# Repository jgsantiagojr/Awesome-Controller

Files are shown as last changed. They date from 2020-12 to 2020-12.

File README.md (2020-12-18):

### Jamie's Awesome Power Controller

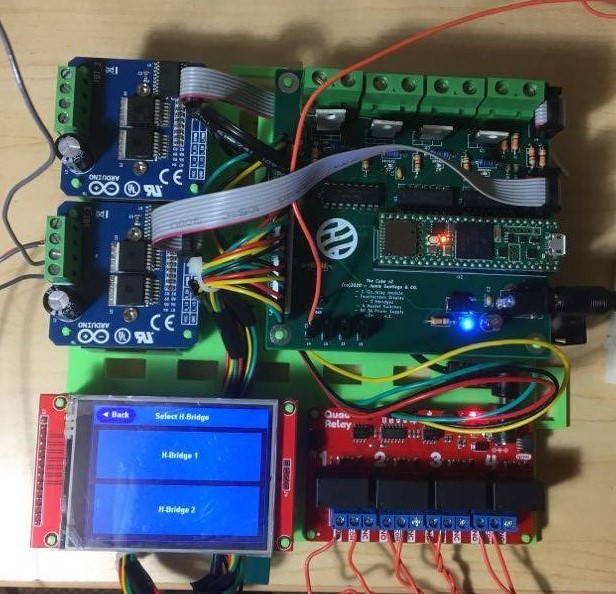
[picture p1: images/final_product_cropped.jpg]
final_product_cropped (https://youtu.be/NAIDJquwWuA "Demo Video")


Hi I'm Jamie! My Awesome Power Controller is a device that is controlled by a Teensy 4.1 and contains 2 H-Bridges, 4 MOSFET switches, and 4 Relays, as well as 4 General Purpose Input Outputs and a Touchscreen Display. Click on the image above for a demo!

The user can choose to either run a pre-written code option or control the different devices independently. An example of a pre-written code option is the Sensor Driven Motor. If the user selects this option, the controller will run a script that sets the PWM signal for H-Bridge 1 to the input from a sensor that is connected to GPIO 14. If the user chooses to control the devices independently then they will be able to individually toggle each of the relays, set the PWM values for each MOSFET switch and set the PWM values and direction for each H-Bridge. 

#### Suppliers

For my PCBs I used: JLCPCB

For my parts I used: Digikey, SparkFun and PJRC

#### Why this project?

This project was originally started for a class I took in the Fall of 2020, Microcontrollers for the Real World.  The point of this class was to be a remote, one-on-one session based class that would teach students to design and build a real-world controller using modular components. I decided that I wanted my project to be something that I could use for future projects and control high power systems with, so I decided to create this generic high power controller. 

#### The Process

##### The Start

The process for this project had a lot of ups and downs. I started off wanting to make everything from scratch and very poorly scoped expectations for what I could do in a semester. But after some initial designs and discussions as to why those designs wouldn't work or what could be better and cheaper, I ended up on a much cleaner path. 

My initial take on the project was that it could be board with a bunch of MOSFETs that the user could configure into different circuits (such as H-bridges and half-bridges) based on what they need to do. It was also supposed to be configurable from the users personal device via Bluetooth in addition to the on-board user interface. However, I quickly learned that this was unnecessarily complex and expensive, and way over-scoped for it to have a reasonable probability of success by the end of the semester. 

So I took a step back. Focused on other things for a day, and came back with a plan. I would use H-bridge modules and then simply have MOSFET switches available as well., in addition to my relay module and touchscreen display. 

##### Prototype 1

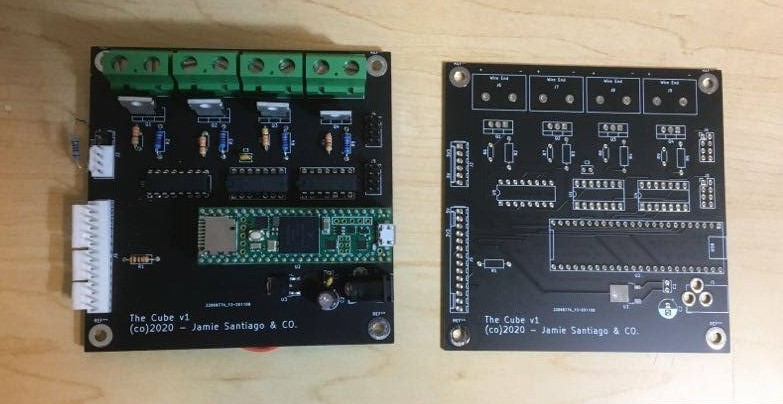
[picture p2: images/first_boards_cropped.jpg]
first_boards_cropped


So a week or two after I pivoted to a more module-focused path, I had my first PCBs shipped. After soldering them together, I saw a few obvious problems:

- There was no way to tell if things were working with just the board, so I needed to add indicator LEDs so I could know if the device I was controlling was working without having to plug in a power source or motor/multimeter and so I could easily tell when the board was on. 
- There was no easy way to connect to ground. When I was trying to test that the right pins were outputting the right things there was no easy ground pin to base the measurements off of. So I needed to add a GND pin. 
- There were no GPIO pins. Had to add those. 
- No ON/OFF Switch, it was on whenever I plugged it in. I didn't like this because I wanted the device to be a tool I could keep on the table-top and that I should be able to turn it off without unplugging it. 

There were also a few problems that weren't so obvious:

- I2C line didn't have pull-up resistors. This made it so the teensy couldn't identify the relay board that I was trying to communicate with. 
- I2C line and the SPI lines shared the SCK pin. This was a big error, since SCK is the SPI clock. I discovered this was the problem after soldering a jumper cable between an SCL pin on the teensy and the clock pin on the I2C line and things started working. So I needed to make sure the I2C line was connected to SCL not SCK.

After I fixed all of these problems in the schematic and updated the layout I was able to send out for my second boards. 

##### Prototype 2

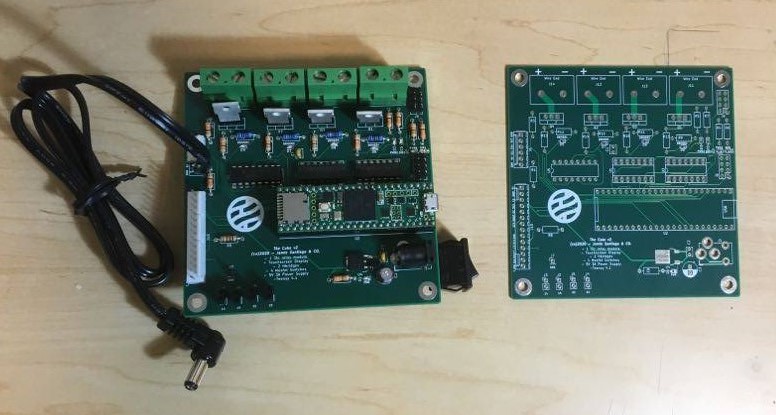
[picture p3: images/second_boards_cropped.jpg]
second_boards_cropped


My second boards were also my final boards. At the same time as ordering them I began designing my mechanical packaging.  The boards worked fairly well but still have a few bugs:

- Something is wrong with the power. Every once in a while the LCD display just shows the backlighting and the only way to fix it is by restarting the entire device. 
- The layout of the board is very awkward. I need to re-lay all the components so that the board integrated more seamlessly with its packaging.
- Having a 6 pin connector for I2C is inconvient when only 4 pins are needed for i2c and the other 2 are for board power. I need to change that from a 6 pin to a 4 pin with a 2 port wire-to-board screw terminal. 

Something that wasn't really a bug but still a pain was the LEDs. They all worked, but since they were tiny and surface mount they took forever to solder on. If there is space to use LEDs that are easier to solder on I need to incorporate them. 

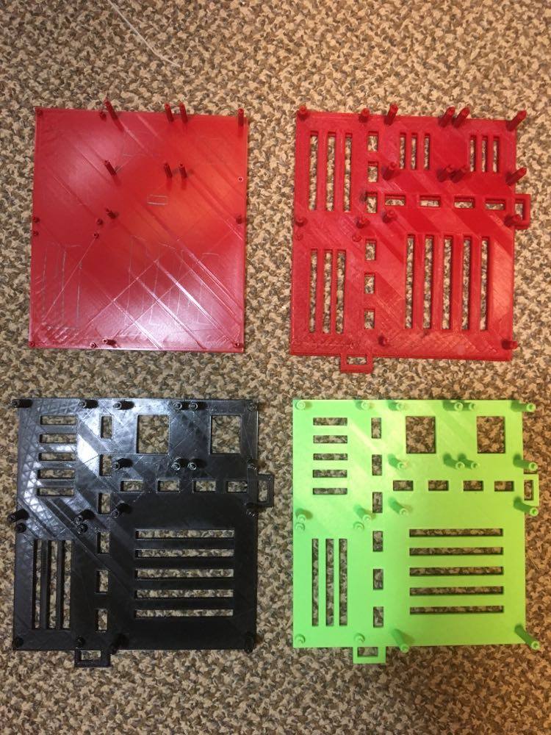
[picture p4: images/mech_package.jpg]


In terms of the mechanical packaging, my first attempt at a design was fun but didn't take into consideration that I would be 3D printing it, so I had to start from the beginning. For what would be my final package, I chose to have a simple plate and pegs to hold all of the modules secure next to each other in a clean way. 

I am proud to say that my second prototype works well and accomplishes what I wanted it to. I definitely learned a lot of circuit board design, mechanical packaging/3D printing and how to tie them in together.  

#### Parts List

| Part Name | Part Number | Price per unit | Distributer |
| --- | --- | --- | --- |
| 2 Pack BTS7940 High Power Driver Module | BTN7960 | 13.89 | Amazon |
| 4 Pack of female 8pos cables | | 8.75 | Amazon |
| 4 Pin Molex Connector | 22232041 | .28 | Digikey |
| 2 Position Wire to Board Terminal | 796739-2 | 1.69 | Digikey |
| 14 Pin Molex Connector | 22232141 | 1.56 | Digikey |
| Power Jack Connector | PJ-202A | .6 | Digikey |
| .1uF Capacitor | C320C104K5R5TA7303 | .22 | Digikey |
| 100uF Capacitor | JMK316ABJ107ML-T | .56 | Digikey |
| Level Converter 16DIP | CD40109BE | .55 | Digikey |
| 8 Position Headers for H-Bridge Module  | PPTC042LFBN-RC | .15 | Digikey |
| 24 Position Headers for Teensy | PPTC241LFBN-RC | 1.37 | Digikey |
| 100 Ohm Resistor | CFR-25JB-52-100R | .1 | Digikey |
| 330 Ohm Resistor | CFR-25JB-52-330R | .1 | Digikey |
| 10K Ohm Resistor | CFR-25JB-52-10K | .1 | Digikey |
| 3v3 1A voltage regulator | NCP1117DT33G | .44 | Digikey |
| 4 Pin Dual-Female Wire | 1597-1502-ND | 3.38 | Digikey |
| 2 Position Headers | S7000-ND | .306 | Digikey |
| LED BLUE CLEAR CHIP SMD | 160-1647-1-ND | .262 | Digikey |
| On-Off switch | 2449-RA1122DWR-ND | .98 | Digikey |
| DC Power Jack | 172-4207-ND | 3.47 | Digikey |
| LCD Touchscreen | DISPLAY_ILI9341_TOUCH | 15 | PJRC |
| Teensy 4.1 | | 26.95 | PJRC |
| Qwiic Quad Relay | COM-16566 | 29.95 | SparkFun |
| 60V N-Channel MOSFETs | FQP30N06L | .95 | SparkFun |

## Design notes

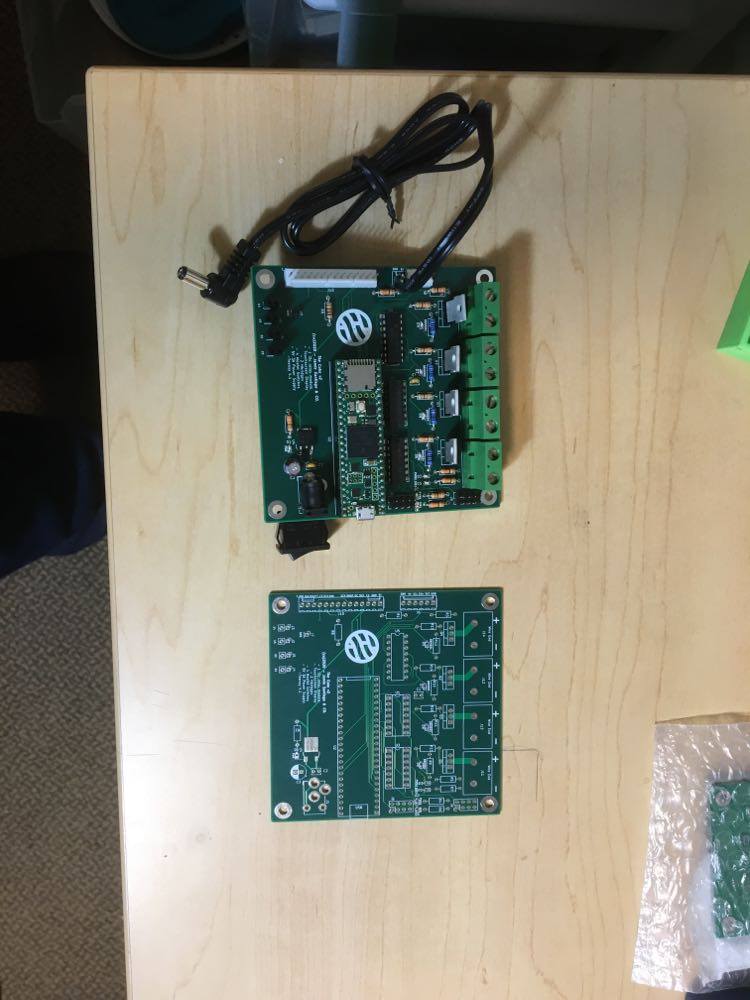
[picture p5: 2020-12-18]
images/second_boards.jpg

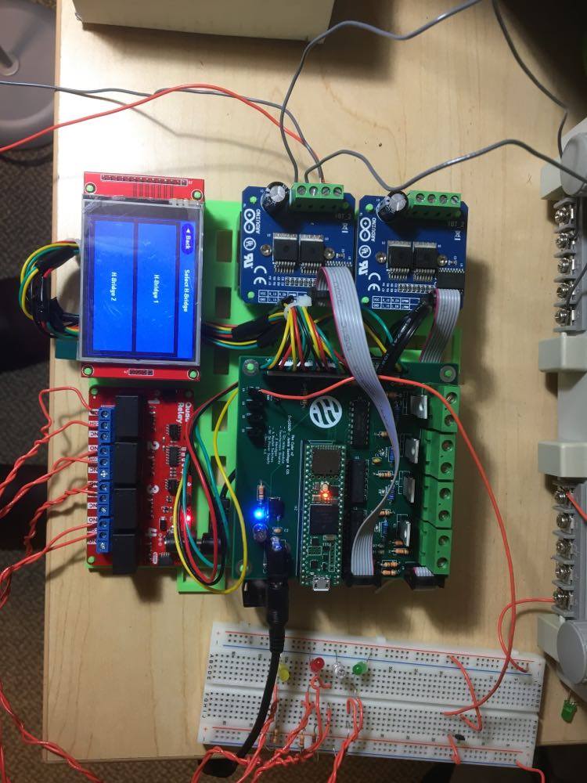
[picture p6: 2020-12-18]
images/final_product.jpg

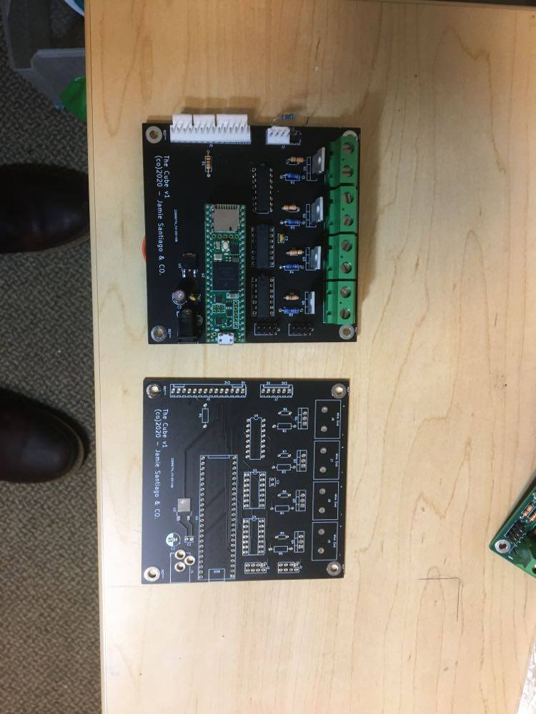
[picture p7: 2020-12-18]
images/first_boards.jpg

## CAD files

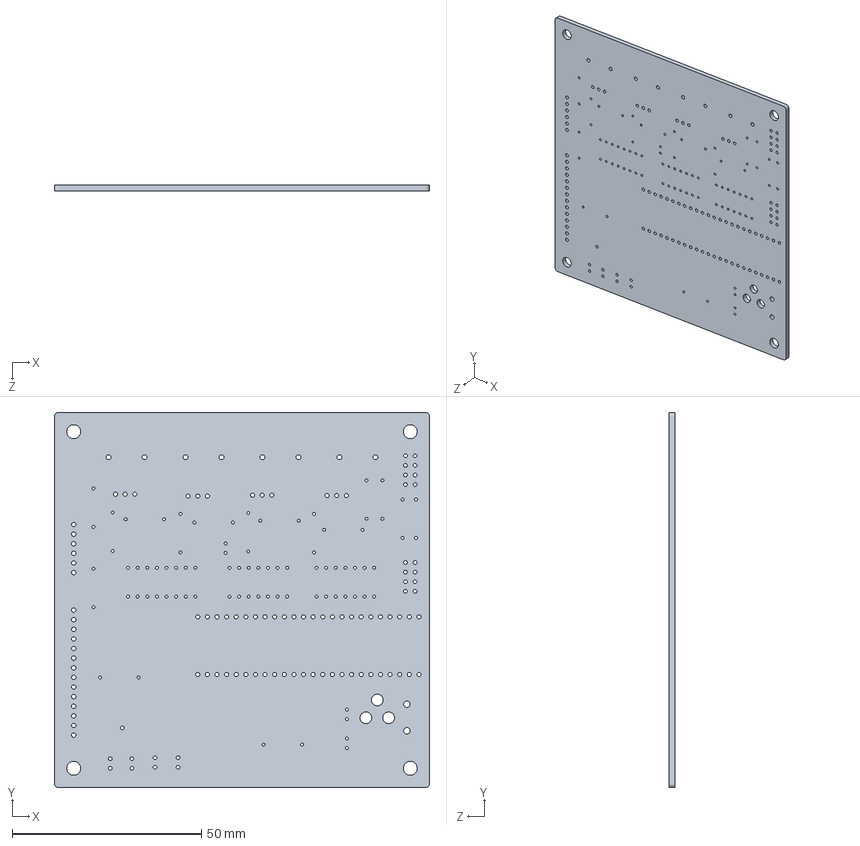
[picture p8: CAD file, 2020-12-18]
Mechanical/Generic_Controller_pcb.SLDPRT
99.1 x 99.1 x 1.60 mm

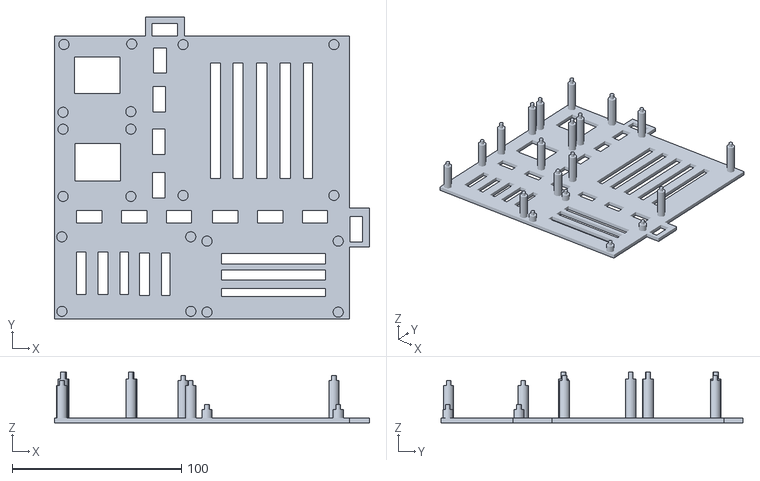
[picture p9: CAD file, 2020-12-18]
Mechanical/STLs/baseplatev5.STL
185.9 x 178.2 x 30.0

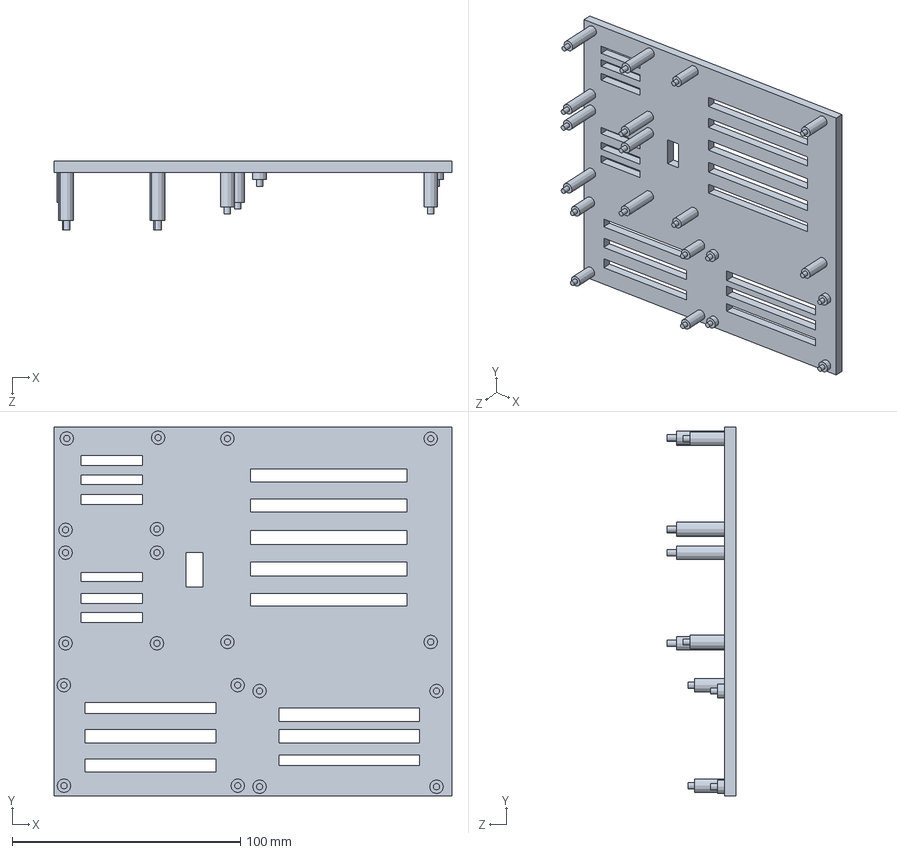
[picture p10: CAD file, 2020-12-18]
Mechanical/baseplate.SLDPRT
174.2 x 161.5 x 30.0 mm

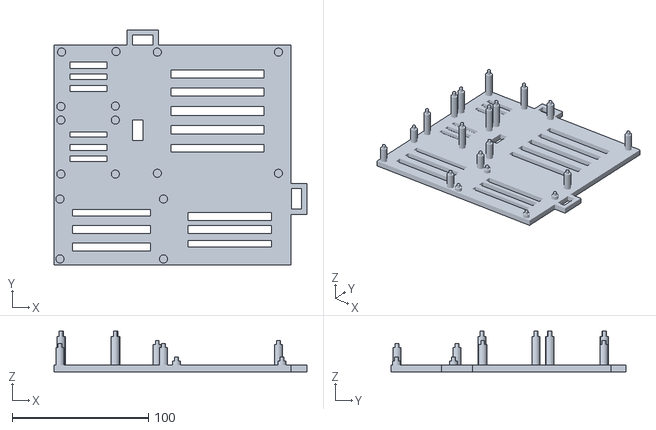
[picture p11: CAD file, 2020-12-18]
Mechanical/STLs/baseplatev2.STL
185.9 x 172.7 x 30.0

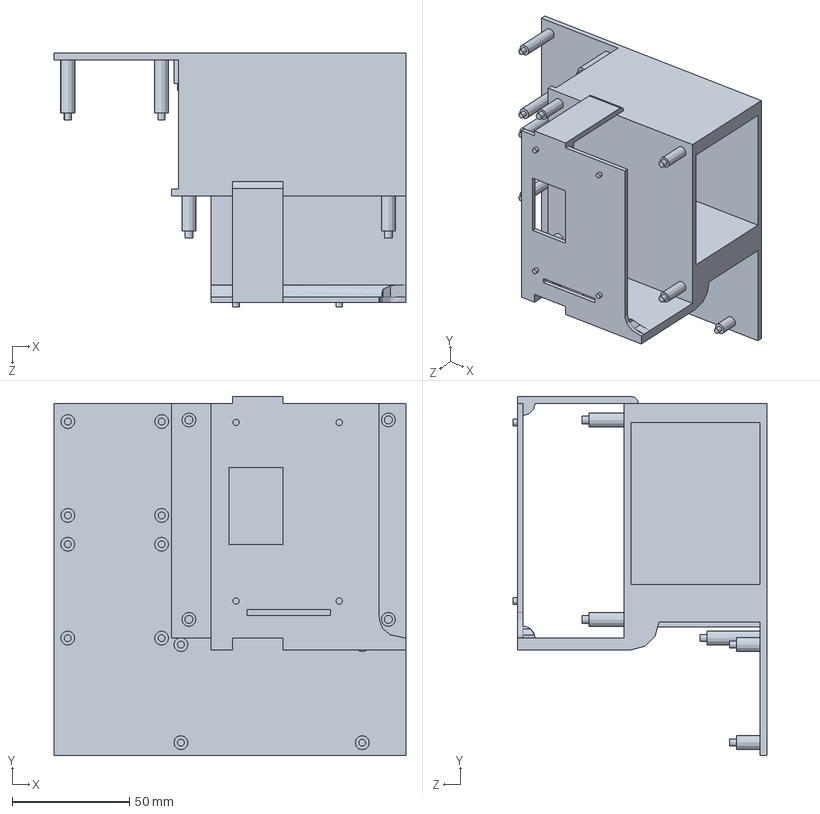
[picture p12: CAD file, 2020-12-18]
Mechanical/PyramidPackage.SLDPRT
150.0 x 153.0 x 108.4 mm

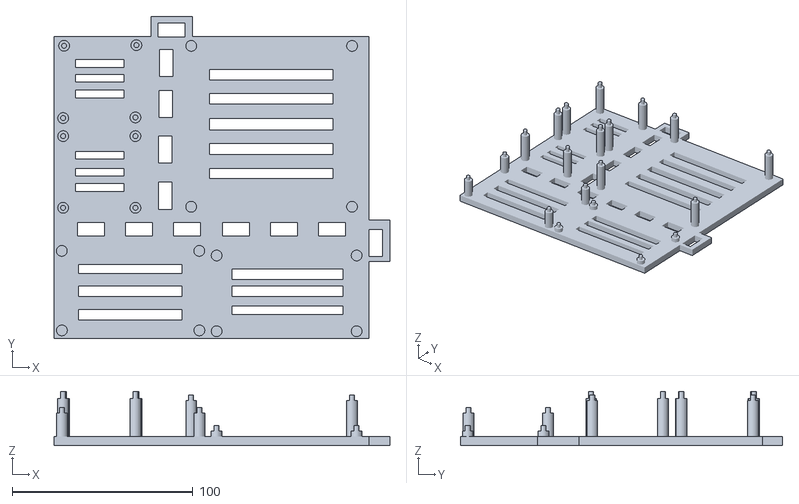
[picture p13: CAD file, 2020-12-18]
Mechanical/STLs/baseplatev4.STL
185.9 x 178.2 x 30.0

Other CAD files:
Mechanical/STLs/baseplatev6.STL
Mechanical/baseplatev3.SLDPRT
Mechanical/STLs/PyramidPackage.STL
Mechanical/STLs/baseplate.STL
Mechanical/STLs/baseplatev3.STL
Mechanical/module_layout.SLDDRW

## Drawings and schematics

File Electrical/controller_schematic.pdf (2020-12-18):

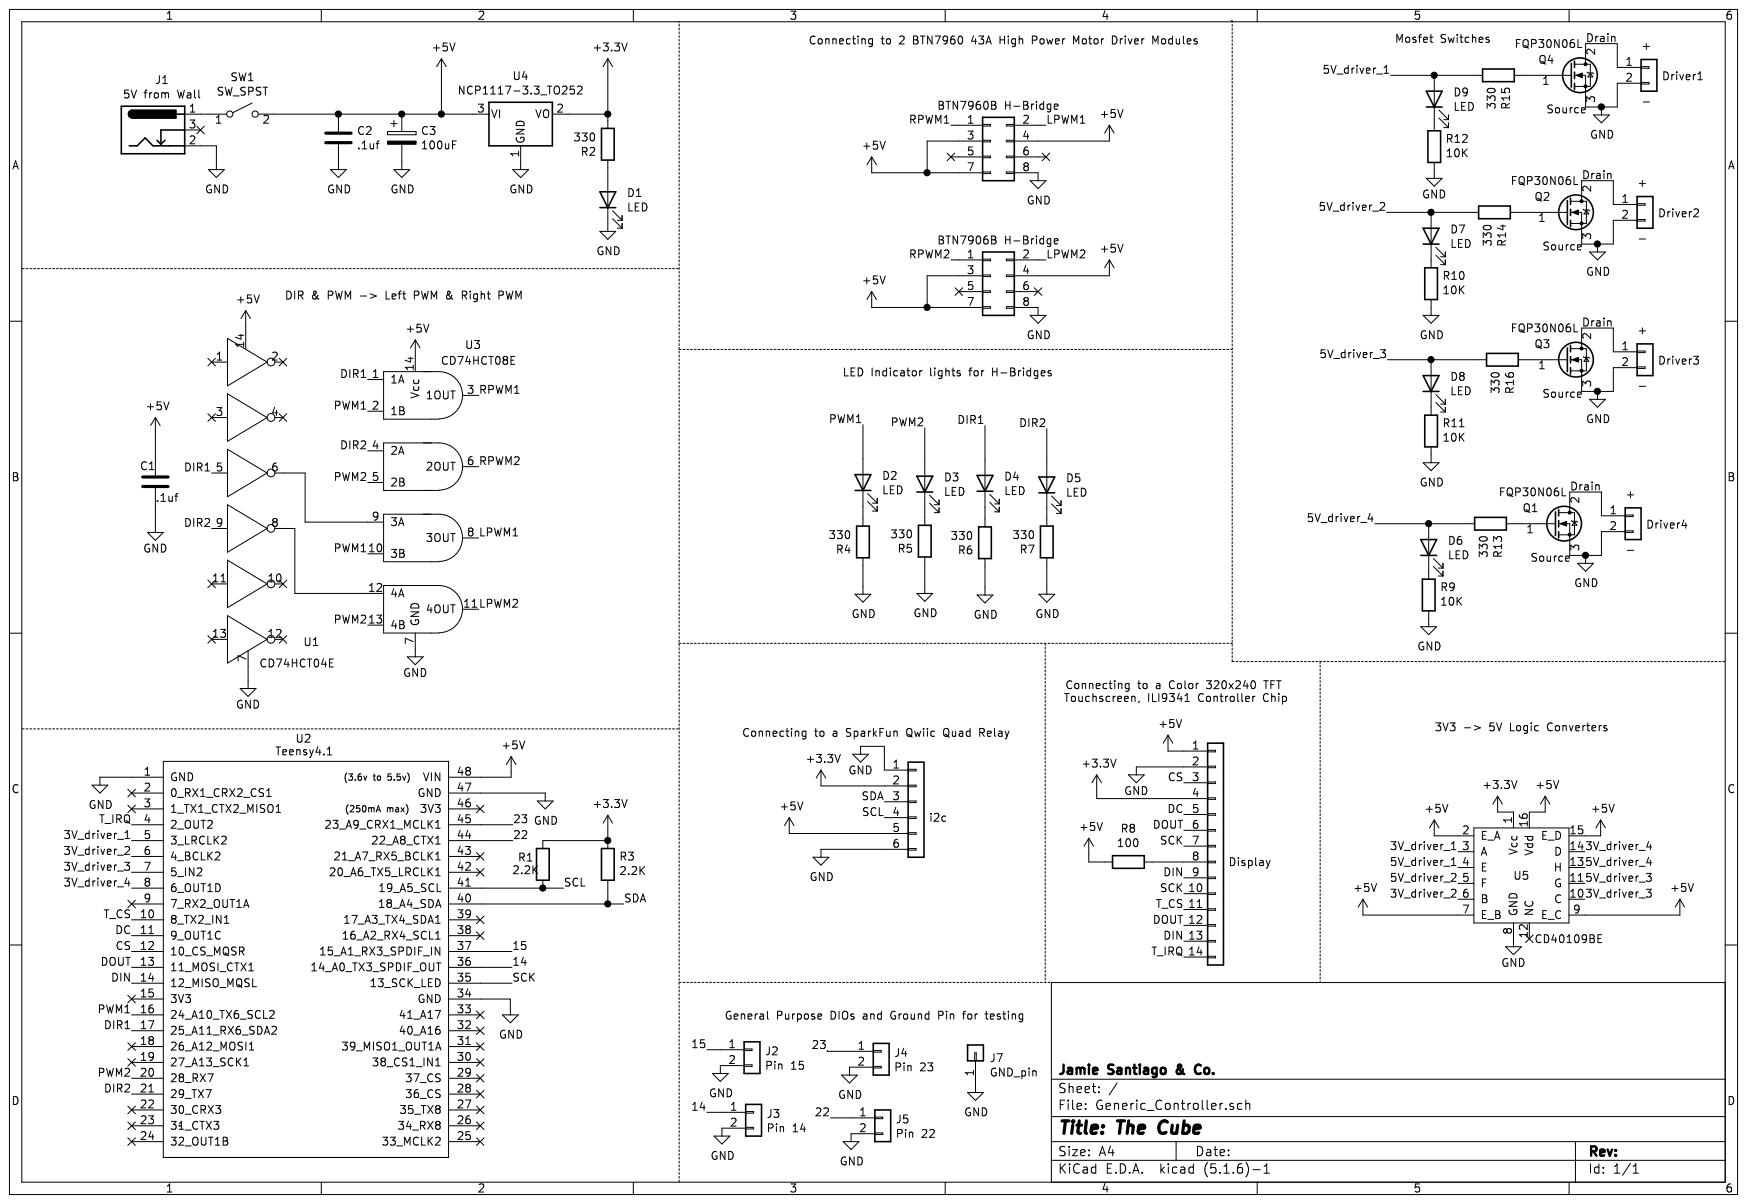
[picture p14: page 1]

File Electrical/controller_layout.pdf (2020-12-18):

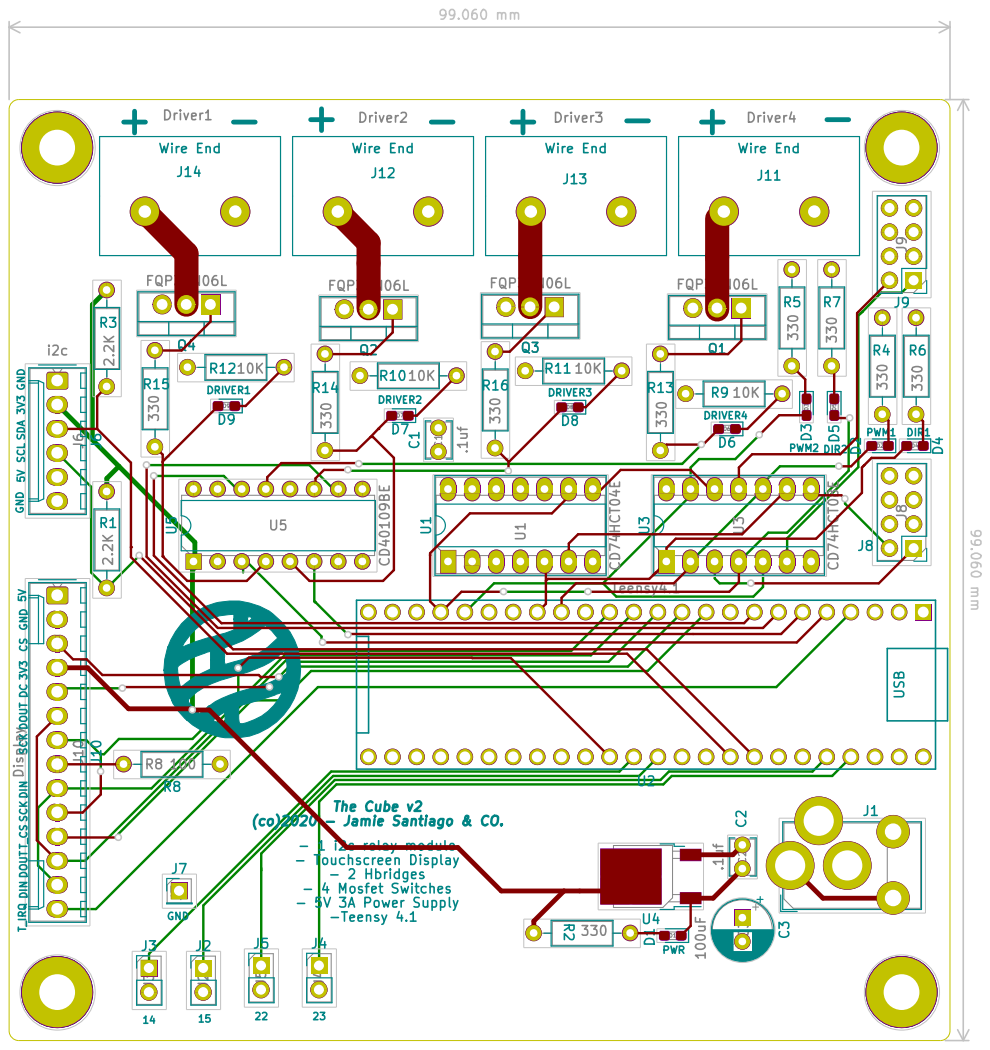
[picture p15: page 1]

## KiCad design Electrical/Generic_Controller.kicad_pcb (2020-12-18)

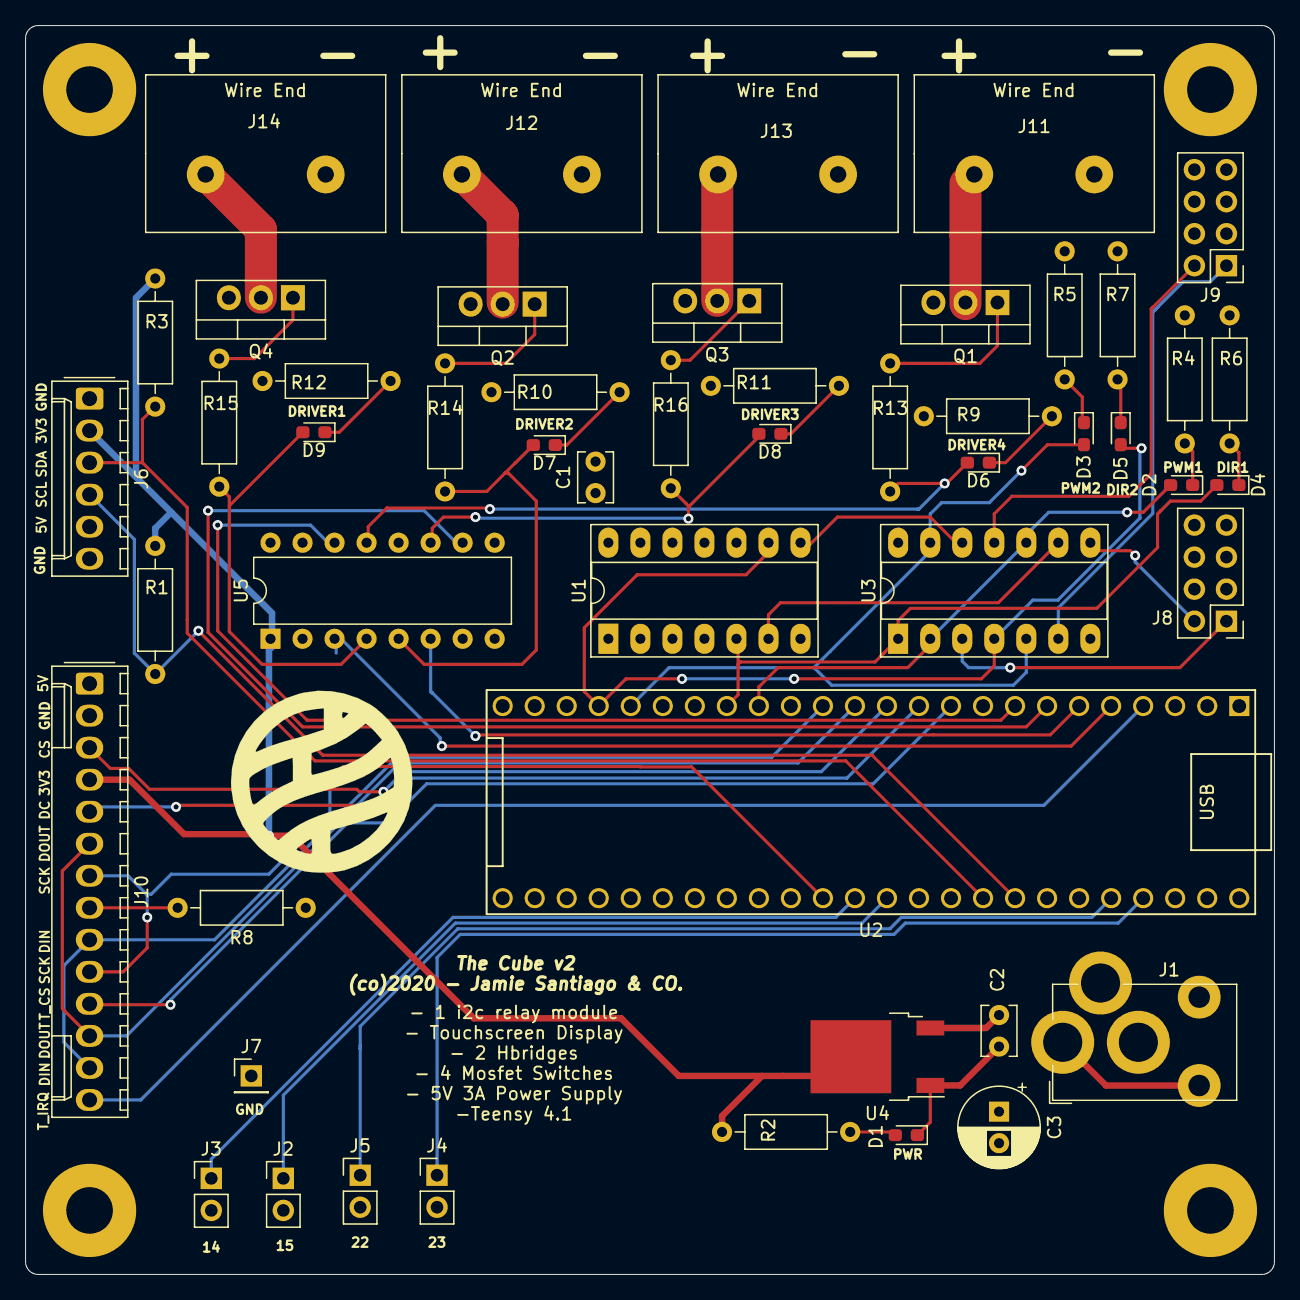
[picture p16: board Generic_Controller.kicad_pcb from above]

Board: 4 copper layers, 99.1 x 99.1 mm, 52 parts (1 on the bottom side), 53 nets.

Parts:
C1, C2: .1uf; C_Disc_D3.8mm_W2.6mm_P2.50mm
C3: 100uF; CP_Radial_D6.3mm_P2.50mm
D1, D2, D3, D4, D5, D6, D7, D8, D9: LED; LED_0603_1608Metric_Pad1.05x0.95mm_HandSolder
J1: 5V from Wall; BarrelJack_Horizontal_3.1mmHole
J2: Pin 15; PinHeader_1x02_P2.54mm_Vertical
J3: Pin 14; PinHeader_1x02_P2.54mm_Vertical
J4: Pin 23; PinHeader_1x02_P2.54mm_Vertical
J5: Pin 22; PinHeader_1x02_P2.54mm_Vertical
J6: i2c; Molex_KK-254_AE-6410-06A_1x06_P2.54mm_Vertical
J7: GND_pin; PinHeader_1x01_P2.54mm_Vertical
J8: BTN7960B H-Bridge; PinHeader_2x04_P2.54mm_Vertical
J9: BTN7906B H-Bridge; PinHeader_2x04_P2.54mm_Vertical
J10: Display; Molex_KK-254_AE-6410-14A_1x14_P2.54mm_Vertical
J11: Driver4; 30A_WireToBoard_796739
J12: Driver2; 30A_WireToBoard_796739
J13: Driver3; 30A_WireToBoard_796739
J14: Driver1; 30A_WireToBoard_796739
Q1, Q2, Q3, Q4: FQP30N06L; TO-220-3_Vertical
R1, R3: 2.2K; R_Axial_DIN0207_L6.3mm_D2.5mm_P10.16mm_Horizontal
R2, R4, R5, R6, R7, R13, R14, R15, R16: 330; R_Axial_DIN0207_L6.3mm_D2.5mm_P10.16mm_Horizontal
R8: 100; R_Axial_DIN0207_L6.3mm_D2.5mm_P10.16mm_Horizontal
R9, R10, R11, R12: 10K; R_Axial_DIN0207_L6.3mm_D2.5mm_P10.16mm_Horizontal
SW1: SW_SPST; rockerSPST
U1: CD74HCT04E; DIP-14_W7.62mm_Socket_LongPads
U2: Teensy4.1; Teensy41
U3: CD74HCT08E; DIP-14_W7.62mm_Socket_LongPads
U4: NCP1117-3.3_TO252; TO-252-2
U5: CD40109BE; DIP-16_W7.62mm

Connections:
+3V3: J6.2, J10.4, R1.2, R2.1, R3.2, U4.2, U5.1
+5V: C1.1, C2.1, C3.1, J6.5, J8.3, J8.4, J8.7, J9.3, J9.4, J9.7, J10.1, R8.1, SW1.2, U1.14, U2.48, U3.14, U4.3, U5.2, U5.7, U5.9, U5.15, U5.16
/3V_driver_1: U2.5, U5.3
/3V_driver_2: U2.6, U5.6
/3V_driver_3: U2.7, U5.10
/3V_driver_4: U2.8, U5.14
/5V_driver_1: D9.2, R15.1, U5.4
/5V_driver_2: D7.2, R14.1, U5.5
/5V_driver_3: D8.2, R16.1, U5.11
/5V_driver_4: D6.2, R13.1, U5.13
/14: J3.1, U2.36
/15: J2.1, U2.37
/22: J5.1, U2.44
/23: J4.1, U2.45
/CS: J10.3, U2.12
/DC: J10.5, U2.11
/DIN: J10.9, J10.13, U2.14
/DIR1: D4.2, U1.5, U2.17, U3.1
/DIR2: D5.2, U1.9, U2.21, U3.4
/DOUT: J10.6, J10.12, U2.13
/LPWM1: J8.2, U3.8
/LPWM2: J9.2, U3.11
/PWM1: D2.2, U2.16, U3.2, U3.10
/PWM2: D3.2, U2.20, U3.5, U3.13
/RPWM1: J8.1, U3.3
/RPWM2: J9.1, U3.6
/SCK: J10.7, J10.10, U2.35
/SCL: J6.4, R1.1, U2.41
/SDA: J6.3, R3.1, U2.40
/T_CS: J10.11, U2.10
/T_IRQ: J10.14, U2.4
GND: C1.2, C2.2, C3.2, D1.1, J1.2, J2.2, J3.2, J4.2, J5.2, J6.1, J6.6, J7.1, J8.8, J9.8, J10.2, J11.2, J12.2, J13.2, J14.2, Q1.3, Q2.3, Q3.3, Q4.3, R4.2, R5.2, R6.2, R7.2, R9.1, R10.1, R11.1, R12.1, U1.7, U2.1, U2.34, U2.47, U3.7, U4.1, U5.8
unnamed: D1.2, R2.2
unnamed: D2.1, R4.1
unnamed: D3.1, R5.1
unnamed: D4.1, R6.1
unnamed: D5.1, R7.1
unnamed: D6.1, R9.2
unnamed: D7.1, R10.2
unnamed: D8.1, R11.2
unnamed: D9.1, R12.2
unnamed: J1.1, SW1.1
unnamed: J10.8, R8.2
unnamed: J11.1, Q1.2
unnamed: J12.1, Q2.2
unnamed: J13.1, Q3.2
unnamed: J14.1, Q4.2
unnamed: Q1.1, R13.2
unnamed: Q2.1, R14.2
unnamed: Q3.1, R16.2
unnamed: Q4.1, R15.2
unnamed: U1.6, U3.9
unnamed: U1.8, U3.12

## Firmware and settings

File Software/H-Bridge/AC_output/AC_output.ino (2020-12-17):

int RPWM_Output = 11; // Arduino PWM output pin 11; connect to IBT-2 pin 1 (RPWM)
int LPWM_Output = 10; // Arduino PWM output pin 6; connect to IBT-2 pin 2 (LPWM)

int spot = 0; //value representing PWM Signal being sent
int state = 0;
boolean dir = true; //whether spot is inscreasing or decreasing 

void setup(){
  pinMode(RPWM_Output,OUTPUT);
//  pinMode(R_EN, OUTPUT);
//  pinMode(R_IS, INPUT);
  
  pinMode(LPWM_Output,OUTPUT);
//  pinMode(L_EN, OUTPUT);
//  pinMode(L_IS, INPUT);

  Serial.begin(9600);
  
}
void loop()
{
  if(state = 0){
    spot = 1023;
    dir = true;
    state = 1;
  }
  else if(state = 1){
    spot = 512;
    if(dir){
      state = 2;  
    }
    else{
      state = 0;
    }
  } 
  else if(state = 2){
    spot = 0;
    dir = false;
    state = 1;
  }

//   digitalWrite(R_EN, HIGH);
//   digitalWrite(L_EN, HIGH);
  spot = 1023;
  // sensor value is in the range 0 to 1023
  // the lower half of it we use for reverse rotation; the upper half for forward rotation 
  if(spot <512){ 
    // reverse rotation
    int reversePWM = -(spot -511)/2;
    analogWrite(LPWM_Output,reversePWM);
    digitalWrite(RPWM_Output, LOW);
    Serial.println("LEFT");
  }
  else
  {
    // forward rotation
    int forwardPWM =(spot -512)/2;
    digitalWrite(LPWM_Output,LOW);
    analogWrite(RPWM_Output,forwardPWM);
    Serial.println("RIGHT");
  }

//  l_is = analogRead(L_IS);
//  Serial.print("L_IS: ");
//  Serial.println(l_is);
//  r_is = analogRead(R_IS);
//  Serial.print("R_IS: ");
//  Serial.println(r_is);
  
}

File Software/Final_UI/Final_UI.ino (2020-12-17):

//Libaries needed for LCD Touchscreen
#include <TeensyUserInterface.h>
#include <font_Arial.h>
#include <font_ArialBold.h>


//Libraries needed for Qwiic Relay Board
#include <SparkFun_Qwiic_Relay.h>
#include <Wire.h>

//I2C Address for Qwiic Relay Board
#define RELAY_ADDR 0x6D

int MOS1 = 3;
int MOS2 = 4;
int MOS3 = 5;
int MOS4 = 6;

int hbPWM1 = 24; //Hbridge 1 PWM PIN
int hbDIR1 = 25; //Hbridge 1 Direction PIN

int hbPWM2 = 28; //Hbridge 2 PWM PIN
int hbDIR2 = 29; //Hbridge 2 Direction PIN


//GPIO pins
int pin14 = 14;
int pin15 = 15;
int pin22 = 22;
int pin23 = 23;

TeensyUserInterface ui; // create the user interface object
Qwiic_Relay quadRelay(RELAY_ADDR);// create quadRelay object 


// ---------------------------------------------------------------------------------
//                                 Setup the hardware
// ---------------------------------------------------------------------------------

void setup() 
{
  Serial.begin(115200);
  Wire.begin();
  Wire.setSDA(18);
  Wire.setSCL(19);

  if(!quadRelay.begin()){
    Serial.println("Check connections to Qwiic Relay");
  } 
  else{
    Serial.println("Ready to flip some switches.");
  }

  pinMode(MOS1, OUTPUT);
  pinMode(MOS2, OUTPUT);
  pinMode(MOS3, OUTPUT);
  pinMode(MOS4, OUTPUT);
  pinMode(hbPWM1, OUTPUT);
  pinMode(hbDIR1, OUTPUT);
  pinMode(hbPWM2, OUTPUT);
  pinMode(hbDIR2, OUTPUT);

  ui.begin(LCD_ORIENTATION_LANDSCAPE_4PIN_RIGHT, Arial_9_Bold);// setup the LCD orientation, the default font and initialize the user interface
  
}

extern MENU_ITEM mainMenu[];
extern MENU_ITEM codeMenu[];
extern MENU_ITEM deviceMenu[];
extern MENU_ITEM hBridgeMenu[];
extern MENU_ITEM mosfetMenu[];
extern MENU_ITEM relayMenu[];



//Starting menu
MENU_ITEM mainMenu[] = {
  {MENU_ITEM_TYPE_MAIN_MENU_HEADER,   "Select Device Type",   MENU_COLUMNS_1,            mainMenu},
  {MENU_ITEM_TYPE_SUB_MENU,            "Code Options",                NULL,         codeMenu},
  {MENU_ITEM_TYPE_SUB_MENU,            "Individual Device Control",           NULL,   deviceMenu},
  {MENU_ITEM_TYPE_END_OF_MENU,        "",                            NULL,                      NULL}
};

//the code menu, with the pre-coded options
MENU_ITEM codeMenu[] = {
  {MENU_ITEM_TYPE_SUB_MENU_HEADER,   "Select Code to run",   MENU_COLUMNS_1,            mainMenu},
  {MENU_ITEM_TYPE_COMMAND,            "Sensor Driven Motor", commandSensorDriven,       NULL},
  {MENU_ITEM_TYPE_END_OF_MENU,        "",                    NULL,                      NULL}
};

// the device menu, select the device to control
MENU_ITEM deviceMenu[] = {
  {MENU_ITEM_TYPE_SUB_MENU_HEADER,   "Select Device Type",   MENU_COLUMNS_1,            mainMenu},
  {MENU_ITEM_TYPE_SUB_MENU,            "H-Bridges",                NULL,         hBridgeMenu},
  {MENU_ITEM_TYPE_SUB_MENU,            "Mosfets",           NULL,   mosfetMenu},
  {MENU_ITEM_TYPE_SUB_MENU,            "Relays",           NULL,        relayMenu},
  {MENU_ITEM_TYPE_END_OF_MENU,        "",                            NULL,                      NULL}
};

//HBridge Selection, go to the individual hbridge controls (PWM and DIRECTION)
MENU_ITEM hBridgeMenu[] = {
  {MENU_ITEM_TYPE_SUB_MENU_HEADER,   "Select H-Bridge",   MENU_COLUMNS_1,            deviceMenu},
  {MENU_ITEM_TYPE_COMMAND,            "H-Bridge 1",                commandSetHBridge1,         NULL},
  {MENU_ITEM_TYPE_COMMAND,            "H-Bridge 2",          commandSetHBridge2,   NULL},
  {MENU_ITEM_TYPE_END_OF_MENU,        "",                            NULL,                      NULL}
};

//MOSFET Selection, go to the individual mosfet controls (PWM)
MENU_ITEM mosfetMenu[] = {
  {MENU_ITEM_TYPE_SUB_MENU_HEADER,    "Select Mosfet",   MENU_COLUMNS_1,  deviceMenu},
  {MENU_ITEM_TYPE_COMMAND,            " MOSFET 1",              commandSetMOS1,           NULL},
  {MENU_ITEM_TYPE_COMMAND,            "MOSFET 2",               commandSetMOS2,           NULL},
  {MENU_ITEM_TYPE_COMMAND,            "MOSFET 3",               commandSetMOS3,           NULL},
  {MENU_ITEM_TYPE_COMMAND,            "MOSFET 4",               commandSetMOS4,           NULL},
  {MENU_ITEM_TYPE_END_OF_MENU,        "",                NULL,            NULL}
};

//RELAY Selection and toggle the different relays individually (ON or OFF)
MENU_ITEM relayMenu[] = {
  {MENU_ITEM_TYPE_SUB_MENU_HEADER,    "Select Relay",   MENU_COLUMNS_1,  deviceMenu},
  {MENU_ITEM_TYPE_TOGGLE,            "1",               menuToggleRelay1Callback,            NULL},
  {MENU_ITEM_TYPE_TOGGLE,            "2",               menuToggleRelay2Callback,            NULL},
  {MENU_ITEM_TYPE_TOGGLE,            "3",               menuToggleRelay3Callback,            NULL},
  {MENU_ITEM_TYPE_TOGGLE,            "4",               menuToggleRelay4Callback,            NULL},
  {MENU_ITEM_TYPE_END_OF_MENU,        "",                NULL,            NULL}
};

//
// display the menu, then execute commands selected by the user
//
void loop() 
{  
  ui.displayAndExecuteMenu(mainMenu);
}

// ---------------------------------------------------------------------------------
//                            PRE_WRITTEN SCRIPTS
// ---------------------------------------------------------------------------------
void commandSensorDriven(void)
{
  
  ui.drawTitleBar("Driving HBridge1 on Pin14 input");
  ui.clearDisplaySpace();

  const int numberBoxAndButtonsHeight = 35;
  
  BUTTON backButton    = {"Back",  ui.displaySpaceCenterX+70, ui.displaySpaceBottomY-25,  120 , numberBoxAndButtonsHeight};
  ui.drawButton(backButton);
  
  pinMode(pin14, INPUT);
  int input = 0;
  
  while(true){
        
    input = analogRead(pin14);
    analogWrite(hbPWM1, input);
    digitalWrite(hbDIR1, true);
    
    if (ui.checkForButtonClicked(backButton)){ //BACK TO SUBMENU
      return;
    }
  }
}
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
